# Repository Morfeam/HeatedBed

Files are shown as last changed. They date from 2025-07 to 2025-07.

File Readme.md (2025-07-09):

# Heated Bed Controller for 3d Printer

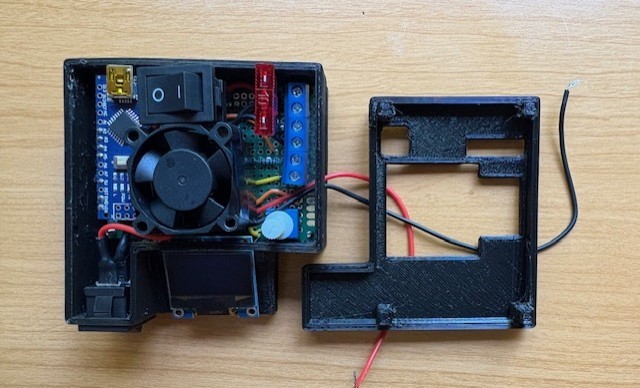
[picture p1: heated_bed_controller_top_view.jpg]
heated bed controller


## Summary

### Backstory

  While building my DIY 3d printer, I've run into several roadblocks along the way. One of which being the temperature read and controlled output of the 3d printers heated bed. Currently, the main controls of my printer (for motor drivers, hotend, LCD display) are run on an arduino mega accompanied by a modified RAMPs 1.4 shield operating at 24 volts (marlin firmware). For whatever reason, after every attempt to drive the heated bed through RAMPs 1.4, my printer would run into several performance issues:
    - Inaccurate readings from bed thermistor
    - Bed continuously heating up, runaway temps well past desired temperature
    - Miscellaneous lapse in readings from hotend thermistor causing hotend temp runaways causing print failures (but only when bed was attached)

  Whether it was the RAMPs 1.4 shield itself, or the bed not playing well with my current setup, I decided to build an additional system to read heated bed temps, set, and hold bed temps via PID Control.

### Reading Temperature

  In order to measure temps, the arduino must measure the voltage at the point past the thermistor and another "known" resistor (voltage-divider). The resistance of the thermistor embedded in my heated bed is approximately 10k ohms. A 10k ohm pull-down resistor is set up and an analog pin is set and gets fed back the voltage at the point past the thermistor + pull-down resistor [see circuit diagram](https://github.com/Morfeam/HeatedBed/tree/main/kicad_files#circuit-diagram-schematic).

  The [Steinhart–Hart equation](https://en.wikipedia.org/wiki/Steinhart%E2%80%93Hart_equation) is used to calculate temperature from the resistance reading on the thermistor.

### Controlling Temperature

  A modified [PID control algorithm](https://en.wikipedia.org/wiki/Proportional%E2%80%93integral%E2%80%93derivative_controller) is used to balance temperatures around a setpoint, where setpoint is the desired temperature and is set via potentiometer.

  The standard output range on the Arduino PWM pin allows for values between 0 - 255. For my purposes, this range in temperature (degrees fahrenheit) works fine, but if higher temps are required I'd recommend driving MOSFET gate by another means (analog pin, optocoupler, etc).

  Arduino drives MOSFET by sending PWM-capped PID values to the MOSFET gate pin (protected by 330R resistor). MOSFET then controls the flow of current from the 24v external power supply to the heated bed, heating it up (Arduino and MOSFET share ground).

  *Warning:* The values saved in [main.cpp](https://github.com/Morfeam/HeatedBed/blob/main/src/main.cpp) were consistently off by 3 degrees fahrenheit of the actual temperature measured by a thermometer I used as a control. A 3 degree fahrenheit error margin is acceptable for my purposes, but it's important to tune the Kp, Ki, and Kd values specific for your setup.

### Output To Display

  OLED display uses I2C protocol and serial communication is handled via the `Adafruit_SSD1306` library to write relevant data to display.

  Display data key:

  Set: *The current set temperature by potentiometer*

  Read: *The current temperature read from thermistor*

  PiD: *current PID value (capped between 0-255 for PWM)*

  Time: *time elapsed in milliseconds*

## Material List

- 1x 50mm x 70mm PCB Prototype Board
- 1x 10 Amp Fuse
- 1x IRF3205 MOSFET
- Solid Core / Jumper Wires (22 AWG)
- 1x Arduino Nano (ATmega328P)
- 1x 10K ohm resistor
- 1x 330R ohm resistor
- 1x 10K potentiometer
- 2x 250V 10A switches
- 1x small OLED display (I2C)
- 3x 2 pin PCB mount screw terminals
- Heatsink for MOSFET
- 2x spade connectors
- Small 12v fan
- 24v heated bed + 10K thermistor
- Soldering setup (iron, solder, etc.)
- External power supply (a means of powering both arduino and heated bed)

#### Optional Materials

- Heat shrink tubing
- 3d printer and PLA filament (for printing the housing)
- Solder flux paste to make better contacts

## Future Enhancements

- Streamline everything to run at 12 volts
  - Currently, my heated bed takes 24 volts while my arduino microcontroller can only support an operating voltage range between 7 - 12 volts.
  - In my case, this isn't too big of an issue, as I already have several components in my DIY printer that require both 12 and 24 volts. However, in the future it would be ideal to have all components functioning at the same voltage.
  - Steamling voltage would reduce complexity of wiring and remove the need for additional power supply / buck converter for arduino.

- Updates to 3d models
  - Models could be updated to better fit the form factor of my printer's design.

- Kicad circuit design to fully milled PCB
    - instead of using wires, this could be done on a custom milled circuit board for reliability, repeatability, and appearance

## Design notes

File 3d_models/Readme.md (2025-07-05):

# Heated Bed Controller - Case Models

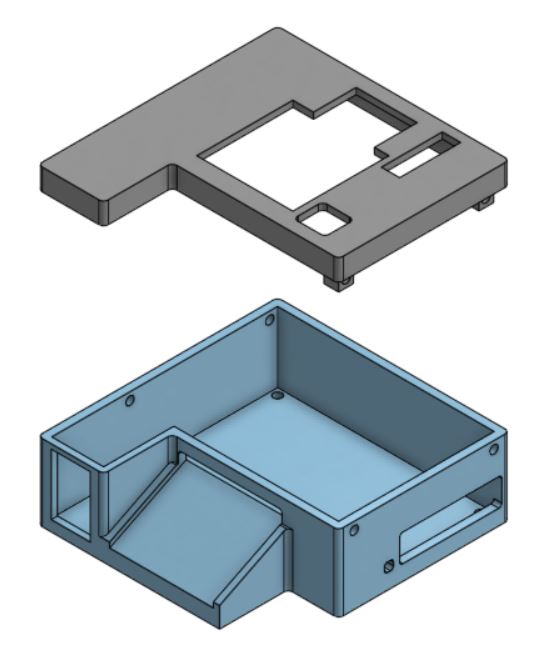
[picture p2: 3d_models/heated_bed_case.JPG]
heated bed case model


- [Link to Onshape Models](https://cad.onshape.com/documents/4e1ef74bedee16f40be708a4/w/d779347fbd50dae2f82cbab2/e/7244d589b04f991c42f21b60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)
- heated-bed-base.stl 
- heated-bed-top.stl

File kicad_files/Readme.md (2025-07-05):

# Heated Bed Controller - KiCad Files and Circuit Diagrm

### Circuit Diagram (Schematic):

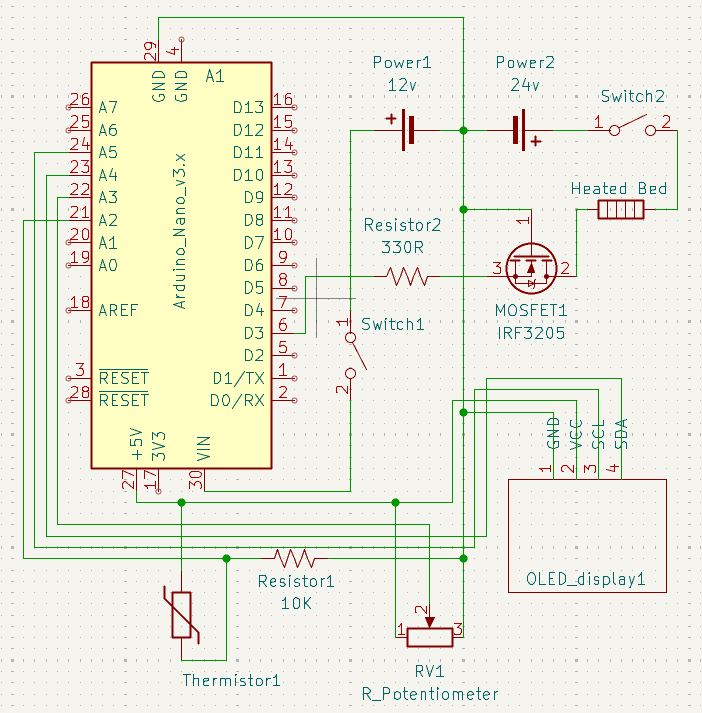
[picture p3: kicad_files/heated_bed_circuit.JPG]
heated bed schematic


### PCB Layout:

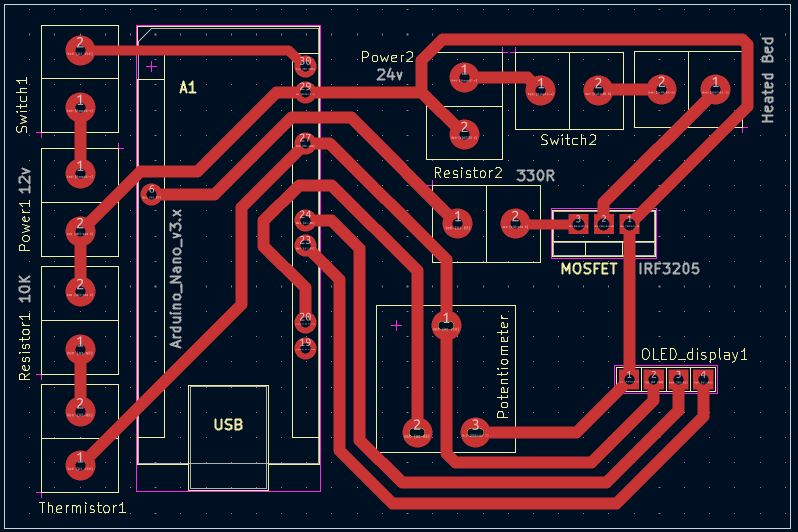
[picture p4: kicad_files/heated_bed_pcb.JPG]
heated bed pcb


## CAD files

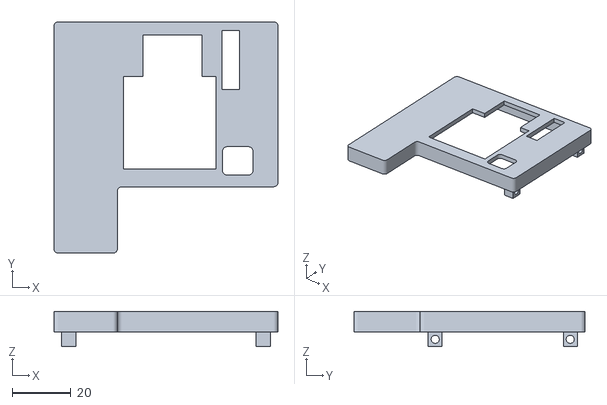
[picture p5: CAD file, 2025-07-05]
3d_models/heated-bed-top.stl
76.0 x 78.5 x 12.0

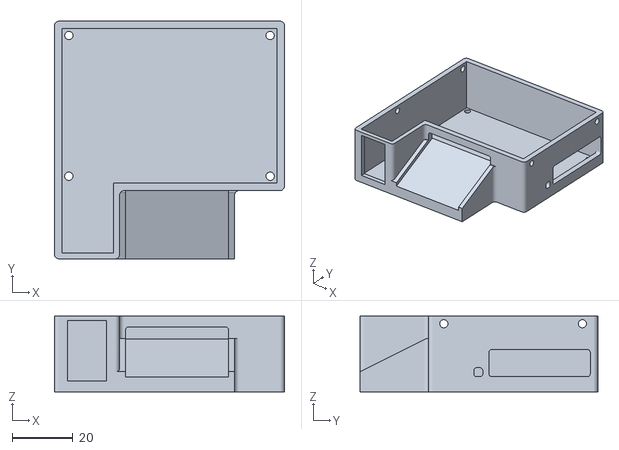
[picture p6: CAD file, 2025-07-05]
3d_models/heated-bed-base.stl
76.0 x 78.5 x 25.0

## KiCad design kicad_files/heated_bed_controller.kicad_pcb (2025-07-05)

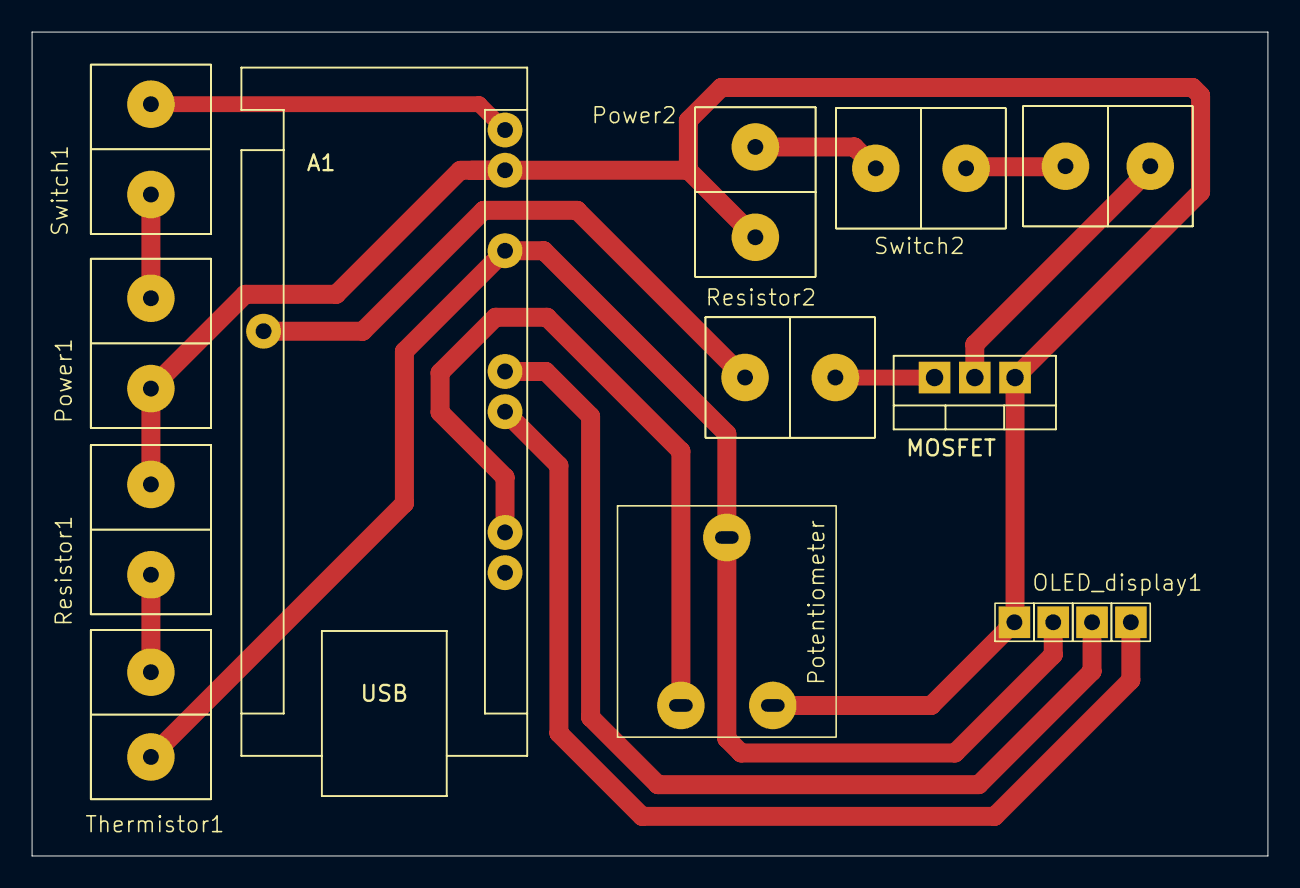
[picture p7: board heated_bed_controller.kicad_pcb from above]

Board: 2 copper layers, 78.0 x 52.0 mm, 12 parts (0 on the bottom side), 12 nets.

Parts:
A1: Arduino_Nano_v3.x; Arduino_Nano
MOSFET: IRF3205; TO-220-3_Vertical
OLED_display1: OLED_display
Potentiometer: R_Potentiometer; arduino_kit_potentiometer
Power1: 12v; screw_mount
Power2: 24v; screw_mount
R2: Heated Bed; screw_mount
Resistor1: 10K; screw_mount
Resistor2: 330R; screw_mount
Switch1, Switch2: SW_SPST; screw_mount
Thermistor1: Thermistor; screw_mount

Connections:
unnamed: A1.27 (+5V), OLED_display1.2 (VCC), Potentiometer.1, Thermistor1.1
unnamed: Resistor1.1, Thermistor1.2
unnamed: A1.23 (A4), OLED_display1.4 (SDA)
unnamed: A1.24 (A5), OLED_display1.3 (SCL)
unnamed: A1.6 (D3), Resistor2.1
unnamed: A1.30 (VIN), Switch1.2 (B)
unnamed: MOSFET.2 (D), R2.1
unnamed: A1.29 (GND), MOSFET.1 (G), OLED_display1.1 (GND), Potentiometer.3, Power1.2 (-), Power2.2 (-), Resistor1.2
unnamed: MOSFET.3 (S), Resistor2.2
unnamed: Power1.1 (+), Switch1.1 (A)
unnamed: Power2.1 (+), Switch2.1 (A)
unnamed: R2.2, Switch2.2 (B)

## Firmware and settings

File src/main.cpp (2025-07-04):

#include <Arduino.h>
#include <Adafruit_SSD1306.h>

#define OLED_RESET 4

// define analog pin connected to potentiometer
const int potPin = A3;

// define digital PWM pin to MOSFET gate
const int PWM_pin = 6;

// define address and config for OLED display
Adafruit_SSD1306 display(OLED_RESET);
const byte SSD1306_ADDR_1 = 0x3C;

int thermistorPin = A2;
int Vo;
float R1 = 10000;
float logR2, R2, T;
float c1 = 1.009249522e-03, c2 = 2.378405444e-04, c3 = 2.019202697e-07;

float set_temperature = 0;
float temperature_read = 0.0;
float PID_error = 0;
float previous_error = 0;
float elapsedTime, Time, timePrev;
float PID_value = 0;

// PID constants
//////////////////////////////////////////////////////////
int kp = 20;   int ki = 0.3;   int kd = 2;
//////////////////////////////////////////////////////////

int PID_p = 0;    int PID_i = 0;    int PID_d = 0;
float last_kp = 0;
float last_ki = 0;
float last_kd = 0;

void setup() {
  // initialize serial communication
  // Serial.begin(9600);

  // initialize display
  display.begin(SSD1306_SWITCHCAPVCC, SSD1306_ADDR_1);
  display.clearDisplay();

  pinMode(PWM_pin, OUTPUT);
}

void loop() {
  // Clear display per iteration then configure text size, cursor, and color
  display.clearDisplay();
  display.setTextSize(1);
  display.setTextColor(WHITE);
  display.setCursor(0,0);

  // Read the analog value from the potentiometer
  set_temperature = analogRead(potPin) / 4;

  /* --UNCOMMENT FOR DEBUGGING POTENTIOMETER-- 
  // Write analog value to MOSFET
  //digitalWrite(6,HIGH);
  analogWrite(PWM_pin,potValue);

  // Print the potentiometer value to the serial monitor
  Serial.print("Potentiometer value: ");
  Serial.println(set_temperature);

  // Print the potentiometer value to OLED display
  display.print("Potentiometer value: "); display.print(set_temperature);
  display.println();
  */ 

  Vo = analogRead(thermistorPin);
  R2 = R1 * (1023.0 / (float)Vo - 1.0);
  logR2 = log(R2);
  T = (1.0 / (c1 + c2*logR2 + c3*logR2*logR2*logR2));
  T = T - 273.15;
  T = (T * 9.0)/ 5.0 + 32.0; 
  temperature_read = T + 90;

  /* --UNCOMMENT FOR DEBUGGING TEMPERATURE READING-- 
  // Print the temperature value to the serial monitor
  Serial.print("Temperature: "); 
  Serial.print(temperature_read);
  Serial.println(" F"); 
  */

  // calculate the error between set temp and real temp
  PID_error = set_temperature - temperature_read;
  // calculate P value
  PID_p = kp * PID_error;
  // calculate I value
  PID_i = PID_i + (ki * PID_error);
  
  timePrev = Time; // the previous time is stored before the actual time read
  Time = millis(); // actual time read
  elapsedTime = (Time - timePrev) / 1000; 
  // calculate D value
  PID_d = kd*((PID_error - previous_error)/elapsedTime);
  // total PID value is the sum of P + I + D
  PID_value = PID_p + PID_i + PID_d;

  // define PWM range between 0 and 255
  if(PID_value < 0)
  {    PID_value = 0;    }
  if(PID_value > 255)  
  {    PID_value = 255;  }
  // write the PWM signal to the mosfet
  analogWrite(PWM_pin,PID_value);
  // store the previous error for next loop
  previous_error = PID_error;

  display.print("PID TEMP control");
  display.println();
  display.print("Set: "); display.print(set_temperature); 
  display.println();
  display.print("Read: "); display.print(temperature_read);
  display.println();
  display.print("PiD: "); display.print(PID_value);
  display.print(" Time: "); display.print(Time);
  display.println();
  display.display();

  // add a small delay for stability
  delay(100);
}

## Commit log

2025-07-04 migrate local heated bed project to repo in github
2025-07-04 add local heated bed project files
2025-07-05 Adds Kicad, 3d models, and documentation
    [heated-bed-base.stl, heated-bed-top.stl, heated_bed_controller.kicad_pcb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]
2025-07-09 correcting resistance in docs
